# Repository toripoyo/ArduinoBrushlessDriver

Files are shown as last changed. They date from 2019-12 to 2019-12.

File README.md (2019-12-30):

Arduino nano を使い、3相ブラシレスモーターを駆動する基板とプログラムです。

## 基板
/KiCad ディレクトリ下に、KiCadプロジェクト一式が保存されています。  
　回路図：Inverter.pdf  
　部品表：PartsList.xlsx  

## 制御プログラム
ArduinoBrushlessDriver下に、Arduinoプロジェクト一式が保存されています。

## 基板の動作
1. 3相ブラシレスモーターをUVW出力端子に接続し、基板に12Vを供給します
1. ボリューム（RV1）を最小位置から1/4ほどの位置にします
1. SW1を押すと、モーターが強制回転され、その後センサレス駆動がはじまります
1. RV1を調整すると、出力電圧が調整でき、回転速度を変えることができます

## モーターに合わせた調整
* 強制回転の際にうまく回らない場合は、RV1を回し、印可電圧を上げて試してみてください。（上げすぎに注意）
* 強制回転を終了する回転数を調整したい場合は、プログラム179行目の定数の値を書き換えてください

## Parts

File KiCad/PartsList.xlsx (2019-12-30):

Reference | Value | Footprint | Datasheet | Description | Manufacturer_Name | Manufacturer_Part_Number
A1 | Arduino_Nano_v3.x | Module:Arduino_Nano | http://www.mouser.com/pdfdocs/Gravitech_Arduino_Nano3_0.pdf
C1 | 47u | Capacitor_THT:CP_Radial_D5.0mm_P2.50mm
C10 | 0.1u | Capacitor_SMD:C_0603_1608Metric_Pad1.05x0.95mm_HandSolder
C11 | 0.1u | Capacitor_SMD:C_0603_1608Metric_Pad1.05x0.95mm_HandSolder
C12 | 10u/35V | Capacitor_THT:CP_Radial_D5.0mm_P2.00mm | ~
C13 | 10u/35V | Capacitor_THT:CP_Radial_D5.0mm_P2.00mm | ~
C14 | 10u/35V | Capacitor_THT:CP_Radial_D5.0mm_P2.00mm | ~
C15 | 0.22u | Capacitor_SMD:C_0603_1608Metric_Pad1.05x0.95mm_HandSolder
C16 | 0.22u | Capacitor_SMD:C_0603_1608Metric_Pad1.05x0.95mm_HandSolder
C17 | 10u/35V | Capacitor_THT:CP_Radial_D5.0mm_P2.00mm | ~
C18 | 10u/35V | Capacitor_THT:CP_Radial_D5.0mm_P2.00mm | ~
C19 | 10u/35V | Capacitor_THT:CP_Radial_D5.0mm_P2.00mm | ~
C2 | 0.1u | Capacitor_SMD:C_0603_1608Metric_Pad1.05x0.95mm_HandSolder
C20 | 0.22u | Capacitor_SMD:C_0603_1608Metric_Pad1.05x0.95mm_HandSolder
C21 | 0.1u | Capacitor_SMD:C_0603_1608Metric_Pad1.05x0.95mm_HandSolder
C22 | 0.1u | Capacitor_SMD:C_0603_1608Metric_Pad1.05x0.95mm_HandSolder
C23 | 0.1u | Capacitor_SMD:C_0603_1608Metric_Pad1.05x0.95mm_HandSolder
C24 | 0.22u | Capacitor_SMD:C_0603_1608Metric_Pad1.05x0.95mm_HandSolder
C25 | 470u | Capacitor_THT:CP_Radial_D12.5mm_P5.00mm
C3 | 0.1u | Capacitor_SMD:C_0603_1608Metric_Pad1.05x0.95mm_HandSolder
C4 | 47u | Capacitor_THT:CP_Radial_D5.0mm_P2.50mm
C5 | 0.1u | Capacitor_SMD:C_0603_1608Metric_Pad1.05x0.95mm_HandSolder
C6 | 470u | Capacitor_THT:CP_Radial_D12.5mm_P5.00mm
C7 | 470u | Capacitor_THT:CP_Radial_D12.5mm_P5.00mm
C8 | 470u | Capacitor_THT:CP_Radial_D12.5mm_P5.00mm
C9 | 0.1u | Capacitor_SMD:C_0603_1608Metric_Pad1.05x0.95mm_HandSolder
D1 | D | Diode_SMD:D_SOD-123 | ~
D2 | D | Diode_SMD:D_SOD-123 | ~
D3 | D | Diode_SMD:D_SOD-123 | ~
D4 | SML-E12P8WT86 | LED_SMD:LED_0603_1608Metric_Pad1.05x0.95mm_HandSolder
D5 | SML-E12P8WT86 | LED_SMD:LED_0603_1608Metric_Pad1.05x0.95mm_HandSolder
D6 | SML-E12P8WT86 | LED_SMD:LED_0603_1608Metric_Pad1.05x0.95mm_HandSolder
D7 | SML-E12P8WT86 | LED_SMD:LED_0603_1608Metric_Pad1.05x0.95mm_HandSolder
H1 | MountingHole_Pad | MountingHole:MountingHole_3.2mm_M3_Pad | ~
H2 | MountingHole_Pad | MountingHole:MountingHole_3.2mm_M3_Pad | ~
H3 | MountingHole_Pad | MountingHole:MountingHole_3.2mm_M3_Pad | ~
H4 | MountingHole_Pad | MountingHole:MountingHole_3.2mm_M3_Pad | ~
IC2 | IRS2003 | SamacSys_Parts:SOIC127P600X175-8N |  | HALF-BRIDGE DRIVER | International Rectifier | IR2104STRPBF
IC3 | IRS2003 | SamacSys_Parts:SOIC127P600X175-8N |  | HALF-BRIDGE DRIVER | International Rectifier | IR2104STRPBF
IC4 | IRS2003 | SamacSys_Parts:SOIC127P600X175-8N |  | HALF-BRIDGE DRIVER | International Rectifier | IR2104STRPBF
P1 | +6 to 24V | Connector_Wire:SolderWirePad_1x01_SMD_5x10mm
P2 | GND | Connector_Wire:SolderWirePad_1x01_SMD_5x10mm
P3 | U | Connector_Wire:SolderWirePad_1x01_SMD_5x10mm
P4 | V | Connector_Wire:SolderWirePad_1x01_SMD_5x10mm
P5 | W | Connector_Wire:SolderWirePad_1x01_SMD_5x10mm
Q1 | NMOS_5V | Package_TO_SOT_SMD:TO-252-3_TabPin2
Q2 | NMOS_5V | Package_TO_SOT_SMD:TO-252-3_TabPin2
Q3 | NMOS_5V | Package_TO_SOT_SMD:TO-252-3_TabPin2
Q4 | NMOS_5V | Package_TO_SOT_SMD:TO-252-3_TabPin2
Q5 | NMOS_5V | Package_TO_SOT_SMD:TO-252-3_TabPin2
Q6 | NMOS_5V | Package_TO_SOT_SMD:TO-252-3_TabPin2
R1 | 1 | Resistor_THT:R_Axial_DIN0309_L9.0mm_D3.2mm_P2.54mm_Vertical
R10 | 1k | Resistor_SMD:R_0603_1608Metric_Pad1.05x0.95mm_HandSolder
R11 | 10 | Resistor_SMD:R_0603_1608Metric_Pad1.05x0.95mm_HandSolder
R12 | 10 | Resistor_SMD:R_0603_1608Metric_Pad1.05x0.95mm_HandSolder
R13 | 10 | Resistor_SMD:R_0603_1608Metric_Pad1.05x0.95mm_HandSolder
R14 | 10 | Resistor_SMD:R_0603_1608Metric_Pad1.05x0.95mm_HandSolder
R15 | 10 | Resistor_SMD:R_0603_1608Metric_Pad1.05x0.95mm_HandSolder
R16 | 10 | Resistor_SMD:R_0603_1608Metric_Pad1.05x0.95mm_HandSolder
R17 | 4.7k | Resistor_SMD:R_0603_1608Metric_Pad1.05x0.95mm_HandSolder
R18 | 1k | Resistor_SMD:R_0603_1608Metric_Pad1.05x0.95mm_HandSolder
R19 | 4.7k | Resistor_SMD:R_0603_1608Metric_Pad1.05x0.95mm_HandSolder
R2 | 10k | Resistor_SMD:R_0603_1608Metric_Pad1.05x0.95mm_HandSolder
R20 | 1k | Resistor_SMD:R_0603_1608Metric_Pad1.05x0.95mm_HandSolder
R21 | 4.7k | Resistor_SMD:R_0603_1608Metric_Pad1.05x0.95mm_HandSolder
R22 | 1k | Resistor_SMD:R_0603_1608Metric_Pad1.05x0.95mm_HandSolder
R23 | 10k | Resistor_SMD:R_0603_1608Metric_Pad1.05x0.95mm_HandSolder
R24 | 10k | Resistor_SMD:R_0603_1608Metric_Pad1.05x0.95mm_HandSolder
R25 | 10k | Resistor_SMD:R_0603_1608Metric_Pad1.05x0.95mm_HandSolder
R26 | 470 | Resistor_SMD:R_0603_1608Metric_Pad1.05x0.95mm_HandSolder
R27 | 470 | Resistor_SMD:R_0603_1608Metric_Pad1.05x0.95mm_HandSolder
R28 | 470 | Resistor_SMD:R_0603_1608Metric_Pad1.05x0.95mm_HandSolder
R29 | 470 | Resistor_SMD:R_0603_1608Metric_Pad1.05x0.95mm_HandSolder
R3 | 10k | Resistor_SMD:R_0603_1608Metric_Pad1.05x0.95mm_HandSolder
R4 | 10k | Resistor_SMD:R_0603_1608Metric_Pad1.05x0.95mm_HandSolder
R5 | 4.7k | Resistor_SMD:R_0603_1608Metric_Pad1.05x0.95mm_HandSolder
R6 | 1k | Resistor_SMD:R_0603_1608Metric_Pad1.05x0.95mm_HandSolder
R7 | 4.7k | Resistor_SMD:R_0603_1608Metric_Pad1.05x0.95mm_HandSolder
R8 | 1k | Resistor_SMD:R_0603_1608Metric_Pad1.05x0.95mm_HandSolder
R9 | 4.7k | Resistor_SMD:R_0603_1608Metric_Pad1.05x0.95mm_HandSolder
RV1 | 10k | Potentiometer_THT:Potentiometer_Alps_RK09K_Single_Vertical
SW1 | SW_PUSH | Button_Switch_THT:SW_PUSH_6mm
SW2 | SW_PUSH | Button_Switch_THT:SW_PUSH_6mm
TP1 | TestPoint | TestPoint:TestPoint_THTPad_D1.0mm_Drill0.5mm | ~
TP2 | TestPoint | TestPoint:TestPoint_THTPad_D1.0mm_Drill0.5mm | ~
TP3 | TestPoint | TestPoint:TestPoint_THTPad_D1.0mm_Drill0.5mm | ~
TP4 | TestPoint | TestPoint:TestPoint_THTPad_D1.0mm_Drill0.5mm | ~
U1 | 7805 | Package_TO_SOT_SMD:TO-252-3_TabPin2

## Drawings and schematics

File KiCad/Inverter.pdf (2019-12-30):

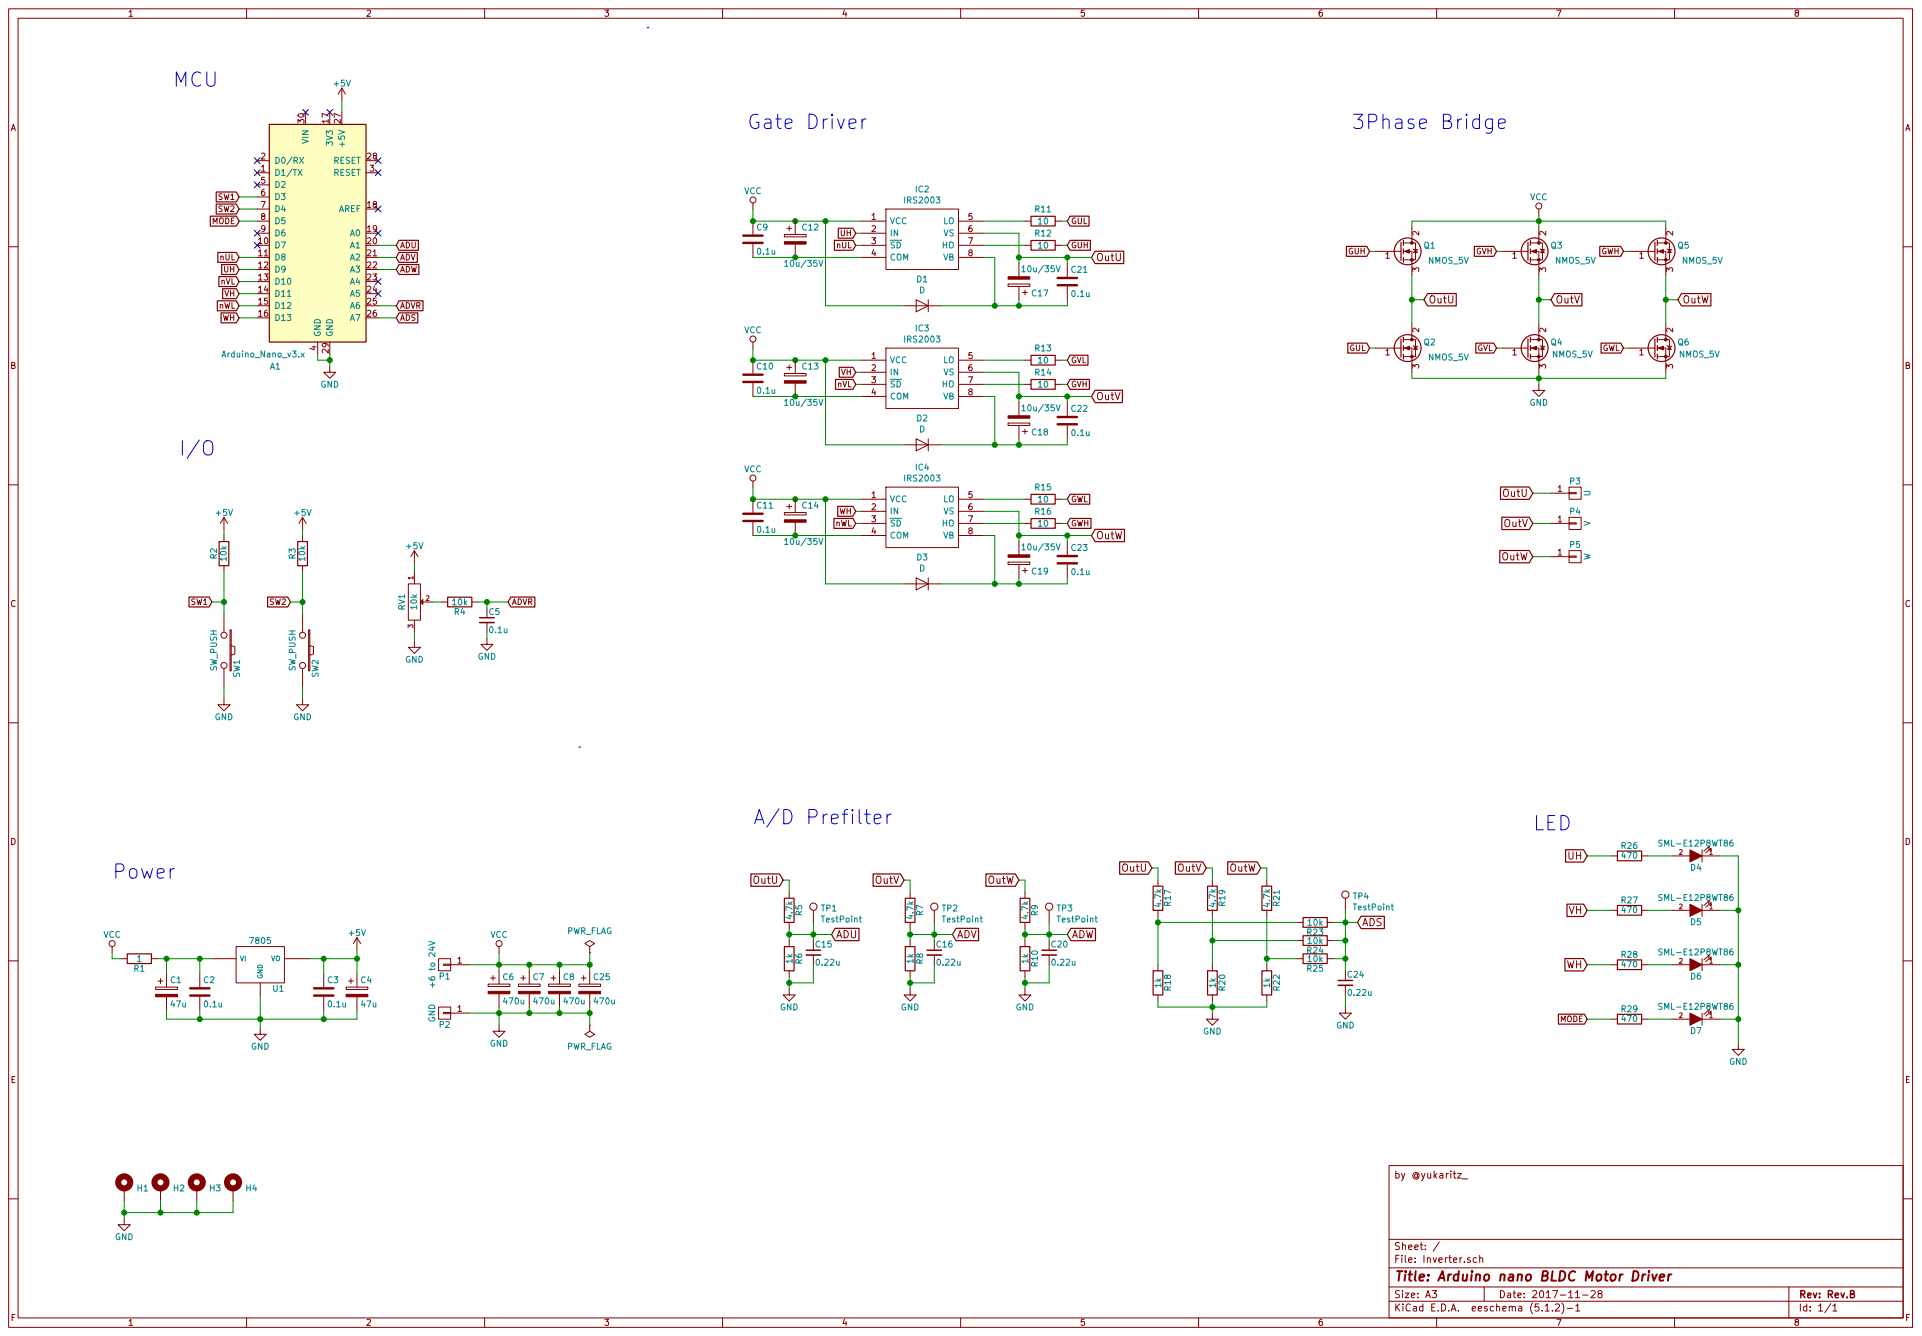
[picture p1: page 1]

Id: 1/1 Title: Arduino nano BLDC Motor Driver File: Inverter.sch Sheet: / by @yukaritz_

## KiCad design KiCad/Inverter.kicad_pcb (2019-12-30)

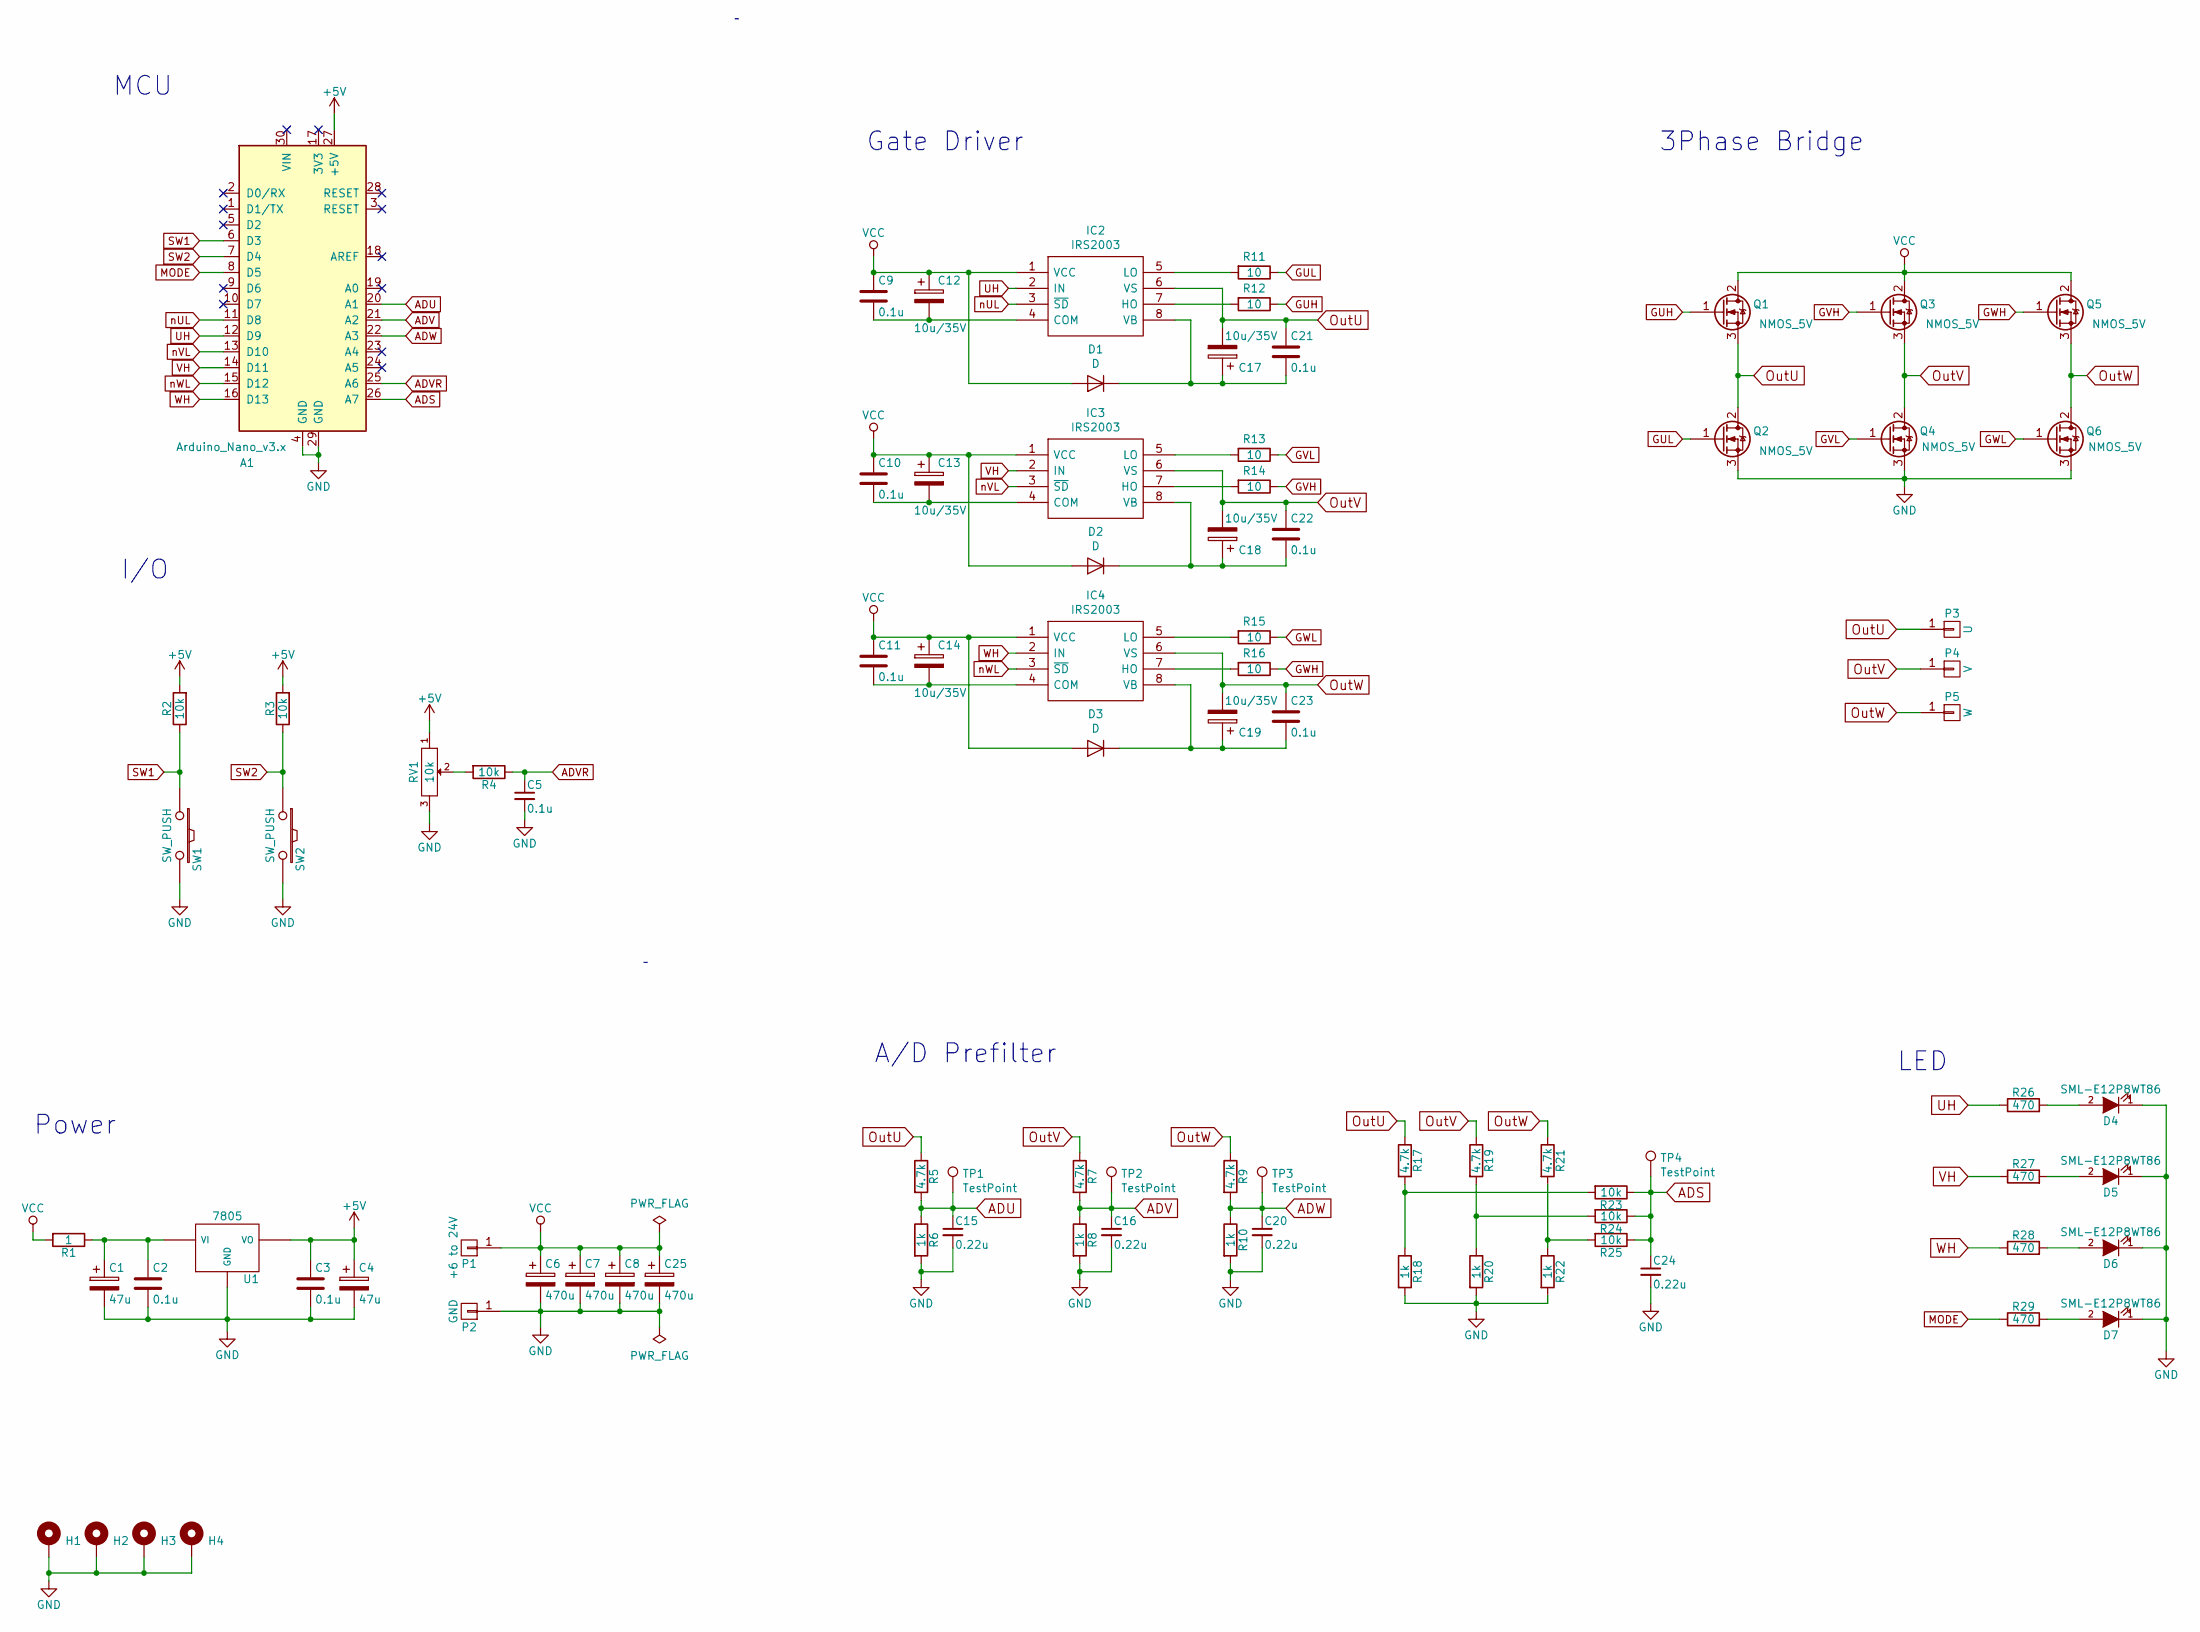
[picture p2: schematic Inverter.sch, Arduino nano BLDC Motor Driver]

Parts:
A1: Arduino_Nano_v3.x; Arduino_Nano
C1, C4: 47u; CP_Radial_D5.0mm_P2.50mm
C2, C3, C5, C9, C10, C11, C21, C22, C23: 0.1u; C_0603_1608Metric_Pad1.05x0.95mm_HandSolder
C6, C7, C8, C25: 470u; CP_Radial_D12.5mm_P5.00mm
C12, C13, C14, C17, C18, C19: 10u/35V; CP_Radial_D5.0mm_P2.00mm
C15, C16, C20, C24: 0.22u; C_0603_1608Metric_Pad1.05x0.95mm_HandSolder
D1, D2, D3: D; D_SOD-123
D4, D5, D6, D7: SML-E12P8WT86; LED_0603_1608Metric_Pad1.05x0.95mm_HandSolder
H1, H2, H3, H4: MountingHole_Pad; MountingHole_3.2mm_M3_Pad
IC2, IC3, IC4: IRS2003; SOIC127P600X175-8N; Manufacturer_Part_Number IR2104STRPBF
P1: +6 to 24V; SolderWirePad_1x01_SMD_5x10mm
P2: GND; SolderWirePad_1x01_SMD_5x10mm
P3: U; SolderWirePad_1x01_SMD_5x10mm
P4: V; SolderWirePad_1x01_SMD_5x10mm
P5: W; SolderWirePad_1x01_SMD_5x10mm
Q1, Q2, Q3, Q4, Q5, Q6: NMOS_5V; TO-252-3_TabPin2
R1: 1; R_Axial_DIN0309_L9.0mm_D3.2mm_P2.54mm_Vertical
R2, R3, R4, R23, R24, R25: 10k; R_0603_1608Metric_Pad1.05x0.95mm_HandSolder
R5, R7, R9, R17, R19, R21: 4.7k; R_0603_1608Metric_Pad1.05x0.95mm_HandSolder
R6, R8, R10, R18, R20, R22: 1k; R_0603_1608Metric_Pad1.05x0.95mm_HandSolder
R11, R12, R13, R14, R15, R16: 10; R_0603_1608Metric_Pad1.05x0.95mm_HandSolder
R26, R27, R28, R29: 470; R_0603_1608Metric_Pad1.05x0.95mm_HandSolder
RV1: 10k; Potentiometer_Alps_RK09K_Single_Vertical
SW1, SW2: SW_PUSH; SW_PUSH_6mm
TP1, TP2, TP3, TP4: TestPoint; TestPoint_THTPad_D1.0mm_Drill0.5mm
U1: 7805; TO-252-3_TabPin2

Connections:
+5V: A1.27 (+5V), C3.1, C4.1, R2.2, R3.2, RV1.1, U1.3 (VO)
ADS: A1.26 (A7), C24.1, R23.1, R24.1, R25.1, TP4.1
ADU: A1.20 (A1), C15.1, R5.2, R6.1, TP1.1
ADV: A1.21 (A2), C16.1, R7.2, R8.1, TP2.1
ADVR: A1.25 (A6), C5.1, R4.1
ADW: A1.22 (A3), C20.1, R9.2, R10.1, TP3.1
GND: A1.4 (GND), A1.29 (GND), C1.2, C2.2, C3.2, C4.2, C5.2, C6.2, C7.2, C8.2, C15.2, C16.2, C20.2, C24.2, C25.2, D4.1 (K), D5.1 (K), D6.1 (K), D7.1 (K), H1.1, H2.1, H3.1, H4.1, P2.1, Q2.3 (S), Q4.3 (S), Q6.3 (S), R6.2, R8.2, R10.2, R18.2, R20.2, R22.2, RV1.3, SW1.2, SW2.2, U1.2 (GND)
GUH: Q1.1 (G), R12.1
GUL: Q2.1 (G), R11.1
GVH: Q3.1 (G), R14.1
GVL: Q4.1 (G), R13.1
GWH: Q5.1 (G), R16.1
GWL: Q6.1 (G), R15.1
MODE: A1.8 (D5), R29.1
unnamed: C1.1, C2.1, R1.1, U1.1 (VI)
unnamed: C10.2, C13.2, IC3.4 (COM)
unnamed: C11.2, C14.2, IC4.4 (COM)
unnamed: C9.2, C12.2, IC2.4 (COM)
unnamed: C17.1, C21.2, D1.1 (K), IC2.8 (VB)
unnamed: C18.1, C22.2, D2.1 (K), IC3.8 (VB)
unnamed: C19.1, C23.2, D3.1 (K), IC4.8 (VB)
unnamed: D4.2 (A), R26.2
unnamed: D5.2 (A), R27.2
unnamed: D6.2 (A), R28.2
unnamed: D7.2 (A), R29.2
unnamed: IC2.5 (LO), R11.2
unnamed: IC2.7 (HO), R12.2
unnamed: IC3.5 (LO), R13.2
unnamed: IC3.7 (HO), R14.2
unnamed: IC4.5 (LO), R15.2
unnamed: IC4.7 (HO), R16.2
unnamed: R4.2, RV1.2
unnamed: R17.2, R18.1, R23.2
unnamed: R19.2, R20.1, R24.2
unnamed: R21.2, R22.1, R25.2
OutU: C17.2, C21.1, IC2.6 (VS), P3.1, Q1.3 (S), Q2.2 (D), R5.1, R17.1
OutV: C18.2, C22.1, IC3.6 (VS), P4.1, Q3.3 (S), Q4.2 (D), R7.1, R19.1
OutW: C19.2, C23.1, IC4.6 (VS), P5.1, Q5.3 (S), Q6.2 (D), R9.1, R21.1
SW1: A1.6 (D3), R2.1, SW1.1
SW2: A1.7 (D4), R3.1, SW2.1
UH: A1.12 (D9), IC2.2 (IN), R26.1
VCC: C6.1, C7.1, C8.1, C9.1, C10.1, C11.1, C12.1, C13.1, C14.1, C25.1, D1.2 (A), D2.2 (A), D3.2 (A), IC2.1 (VCC), IC3.1 (VCC), IC4.1 (VCC), P1.1, Q1.2 (D), Q3.2 (D), Q5.2 (D), R1.2
VH: A1.14 (D11), IC3.2 (IN), R27.1
WH: A1.16 (D13), IC4.2 (IN), R28.1
nUL: A1.11 (D8), IC2.3 (~SD)
nVL: A1.13 (D10), IC3.3 (~SD)
nWL: A1.15 (D12), IC4.3 (~SD)

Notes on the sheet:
MCU
A/D Prefilter
Power
3Phase Bridge
LED
I/O
Gate Driver

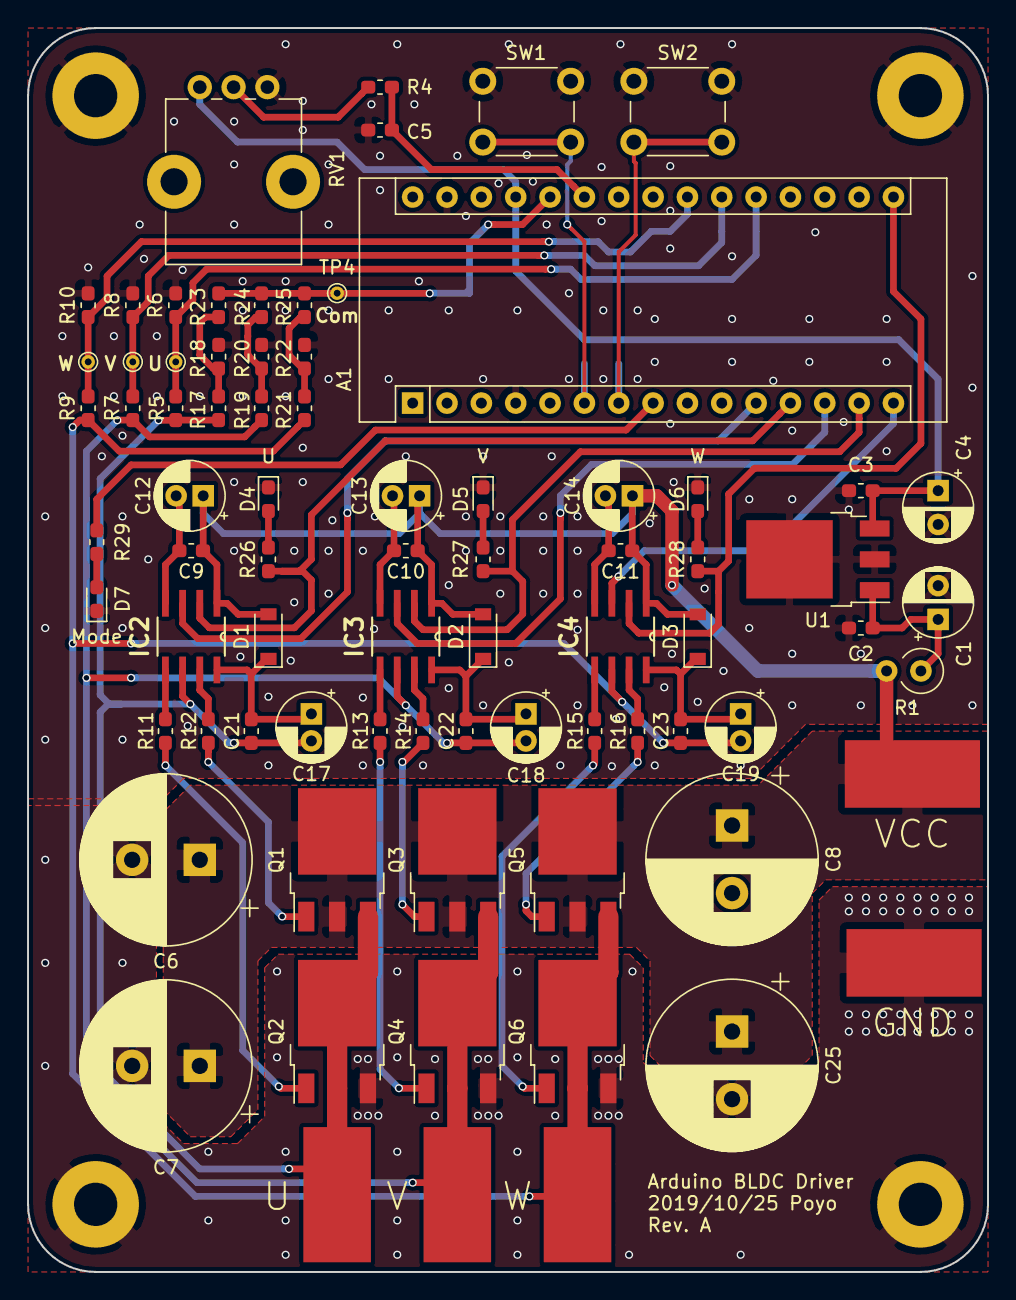
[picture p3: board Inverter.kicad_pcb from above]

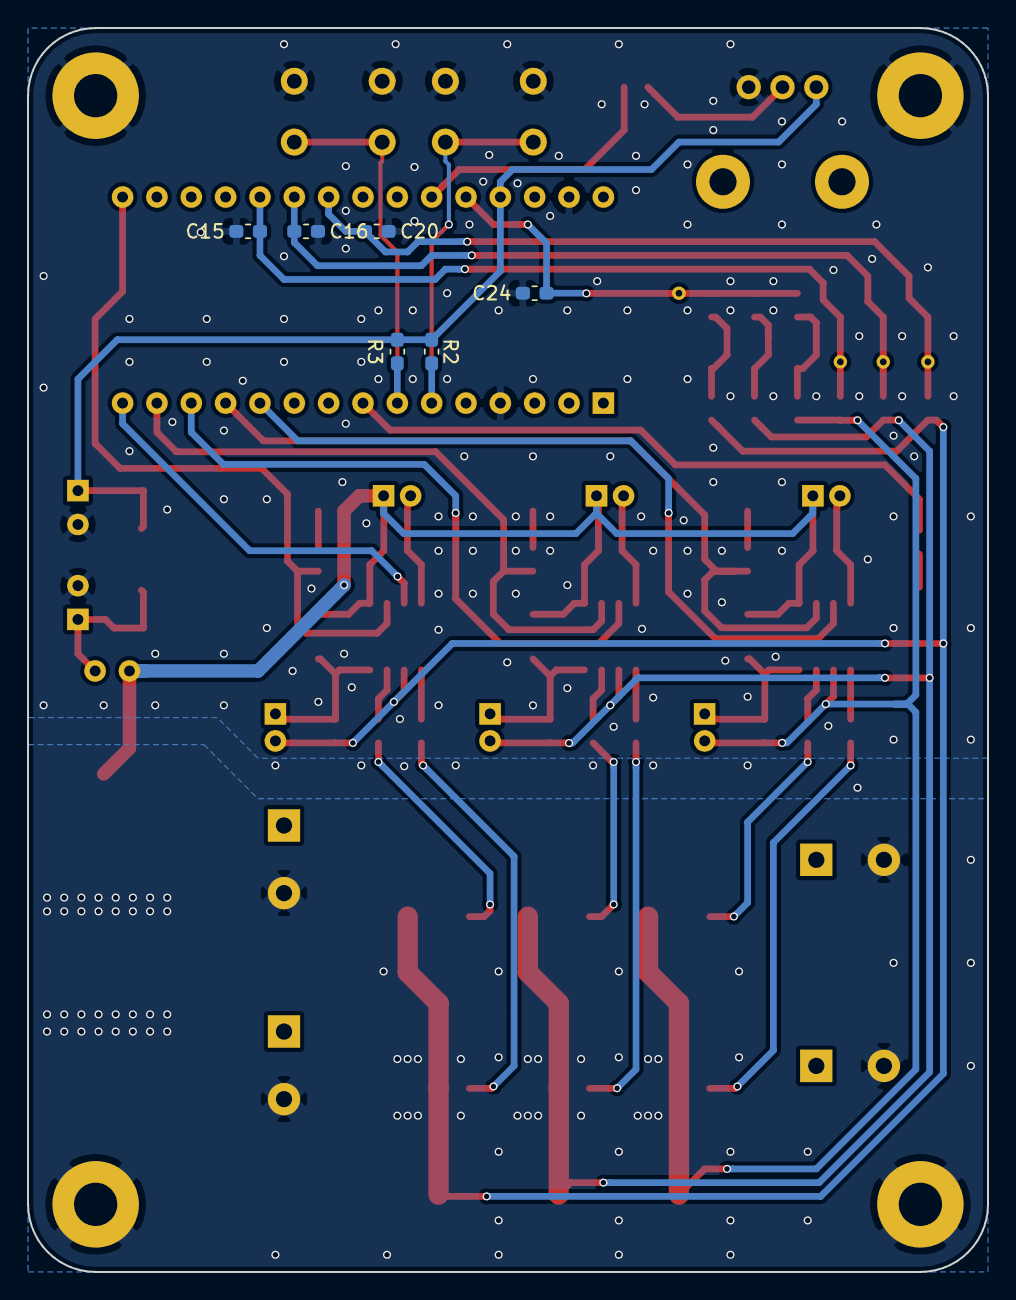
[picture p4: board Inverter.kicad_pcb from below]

Board: 2 copper layers, 71.0 x 92.0 mm, 88 parts (6 on the bottom side), 47 nets.

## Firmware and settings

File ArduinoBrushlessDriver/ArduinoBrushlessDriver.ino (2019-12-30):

// Sensorless Blushless Motor Driver using Arduino nano

// ポートの定義
#define LED_MODE 5
#define SW1 3
#define SW2 4
#define ADVR 6
#define ADS 7
#define OPEN 12
#define BLAKE 13

// ゲートドライバの種類とArduinoのDigitalポートの対応
typedef enum
{
  UL = 8,  // U相ローサイド  PB0
  UU = 9,  // U相ハイサイド  PB1
  VL = 10, // PB2
  VU = 11, // PB3
  WL = 12, // PB4
  WU = 13  // PB5
} GATEDRIVER;

// AD変換するポートとUVW相の関係
typedef enum
{
  AD_U = 1,
  AD_V = 2,
  AD_W = 3
} ADPORT;

// ポートBの状態の定義
const unsigned short int portBStatus[14] = {
    0b00010011, // U -> V（U相High、V相Low、W相Open）
    0b00000111, // U -> W
    0b00001101, // V -> W
    0b00011100, // V -> U
    0b00110100, // W -> U
    0b00110001, // W -> V
    0b00010000, // U(Low) -> V (U相Low、V相Low、W相Open、PWM用)
    0b00000100, // U(Low) -> W
    0b00000001, // V(Low) -> W
    0b00010000, // V(Low) -> U
    0b00000100, // W(Low) -> U
    0b00000001, // W(Low) -> V
    0b00010101, // All off
    0b00000000  // Blake
};

// ある回転位置のときにどの相がオープン状態か
const unsigned short int lookADC[6] = {AD_W, AD_V, AD_U, AD_W, AD_V, AD_U};
unsigned short int curRotorStat = 0; // 現在の回転位置
const unsigned short int forwardTime = 0;

void setup()
{
  // タイマ割り込み設定
  TCCR1A = 0x00;
  TCCR1B = 0b00001001;
  OCR1A = 0x300; // PWM周波数は20kHz (16MHz/0x300)
  OCR1B = 0x0000;

  pinMode(UU, OUTPUT);
  pinMode(VU, OUTPUT);
  pinMode(WU, OUTPUT);
  pinMode(UL, OUTPUT);
  pinMode(VL, OUTPUT);
  pinMode(WL, OUTPUT);
  pinMode(LED_MODE, OUTPUT);
  pinMode(SW1, INPUT);
  pinMode(SW2, INPUT);
  DDRB = 0b00111111;

  pinMode(A1, INPUT);
  pinMode(A2, INPUT);
  pinMode(A3, INPUT);
  pinMode(A6, INPUT);
  pinMode(A7, INPUT);

  // SW1かSW2を押すと駆動スタート
  while (digitalRead(SW1) == HIGH && digitalRead(SW2) == HIGH)
  {
    // 駆動開始まではブレーキ状態にしておく
    PORTB = portBStatus[BLAKE];
  }
  TIMSK1 = 0b00000110; // 割り込み有効にする
  if (digitalRead(SW2) == HIGH)
  {
    startup();
  }
}

// 割り込み処理（手動PWM）
ISR(TIMER1_COMPA_vect)
{
  // PWMのHigh状態
  PORTB = portBStatus[curRotorStat];
}
ISR(TIMER1_COMPB_vect)
{
  // PWMのLow状態
  PORTB = portBStatus[curRotorStat + 6];
}

// 次の回転状態を設定する
void portSwitch()
{
  curRotorStat++;
  if (curRotorStat >= 6)
  {
    curRotorStat = 0;
  }
}

// ビット数を犠牲にした高速AD変換
uint8_t myFastADC(uint8_t port)
{
  ADMUX = 0b01100000 | port;
  ADCSRA = 0b11000011; // AD Clockを2MHzにし、変換開始（7.5bit分解能）
  while (ADCSRA != 0b10010011)
    ; // 変換完了を待機
  return ADCH;
}

// PWM値をボリュームから読み込んで設定する
void setPWMfromVR()
{
  OCR1B = ((0xFF - (myFastADC(ADVR))) << 2) + 0x05;
}

// センサレス制御ループ
bool changeSwitchStatFlag = false; // 次の回転位置に進むフラグ
float rotatePeriod = 0;            // 60度回転する経過時間
unsigned long timeOld = 0;         // 60度回転する経過時間の測定用
int bemf = 0;                      // 誘起電圧

void loop()
{
  // 誘起電圧が中点電圧を横切るタイミングを検出する
  changeSwitchStatFlag = false;
  while (changeSwitchStatFlag == false)
  {
    bemf = (int)myFastADC(lookADC[curRotorStat]) - (int)myFastADC(ADS);
    switch (curRotorStat) // ロータ位置によって逆起電力の方向が異なる
    {
    case 1: // fall through
    case 3:
    case 5:
      if (bemf >= 0)
      {
        changeSwitchStatFlag = true;
      }
      break;
    case 0: // fall through
    case 2:
    case 4:
      if (bemf < 0)
      {
        changeSwitchStatFlag = true;
      }
      break;
    }
  }

  // 誘起電圧が中点電圧を横切ったタイミングで、60度回転するのに要した時間を計測する
  rotatePeriod = (rotatePeriod * 15.0 + micros() - timeOld) / 16; // 60度分の時間の測定

  delayMicroseconds(((int)rotatePeriod >> 1) - forwardTime); // 30度分待機する
  portSwitch();                                              // 磁界を60度回転させる
  timeOld = micros();
  setPWMfromVR();                            // PWMのデューティ比（出力パワー）を設定する
  delayMicroseconds((int)rotatePeriod >> 2); // 転流完了待ち
}

// 強制回転
void startup()
{
  float waitMicroSec = 0;
  float curRev = 0;
  const float maxRev = 15 * 60.0; // 最大の電気的回転数
  const float revAdd = 0.001;     // 回転数の増加スピード

  digitalWrite(LED_MODE, LOW);

  portSwitch();
  delay(500); // ある回転位置でしばらく待つ

  while (curRev < maxRev)
  {
    curRev = curRev + revAdd * waitMicroSec;
    waitMicroSec = 1.0 / (curRev / 60.0) / 6.0 / 3.0 * 100000.0;
    if (waitMicroSec >= 16000)
      waitMicroSec = 16000;
    if (waitMicroSec <= 1)
      waitMicroSec = 1;

    setPWMfromVR();
    portSwitch();

    // delayMicroseconds は 16000us までしか出力できないので、3つ繋げてより長い時間待てるようにする
    delayMicroseconds((int)waitMicroSec);
    delayMicroseconds((int)waitMicroSec);
    delayMicroseconds((int)waitMicroSec);
  }

  digitalWrite(LED_MODE, HIGH);
  rotatePeriod = waitMicroSec * 3;
  timeOld = micros();
}
